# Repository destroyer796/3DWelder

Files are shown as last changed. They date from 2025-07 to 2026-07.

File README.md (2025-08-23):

# 3DWelder
This is an overbuilt 3D pen designed to be used for "welding" 3D printed parts together using 1.75mm filament. This project is funded by [Hack Club](https://hackclub.com/) as a part of the [Highway](https://highway.hackclub.com/) program.

Keep in mind for time being PCB is not working, I'll update soon.

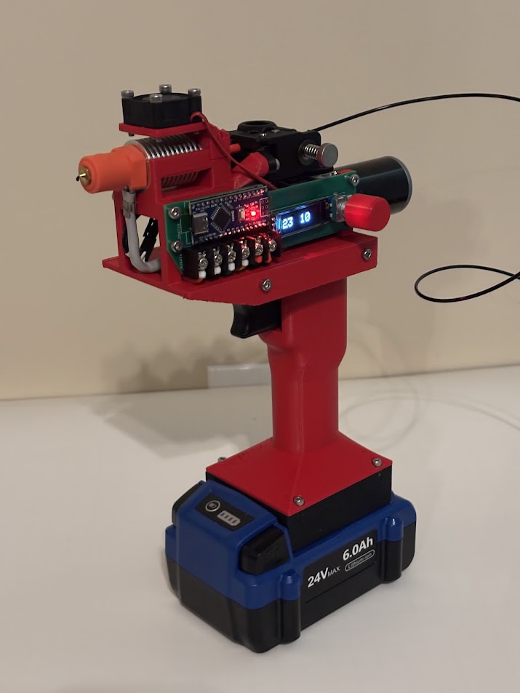
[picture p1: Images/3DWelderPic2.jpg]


This design uses a CHC Pro hotend and a custom Orbiter extruder adapted to use a DC motor. This DC motor's speed is controlled by a drill trigger adapted into the handle. It has a small screen and a rotary encoder for adjusting and showing the temperature target. The whole thing is powered by a drill battery to make it more portable and easier to use. This project is currently completely untested.

## Why?
So, why did I choose to make this ridiculous thing anyways? Well, the best way to join 3D printed parts together if they can't be screwed is by literally joining them together with the same plastic they're made of. This can be very difficult with a normal 3D pen though, as they're quite low powered and actually can't even melt many higher temperature plastics. I wanted a solution to this, so I decided to basically make a regular 3D printer extruding setup, but make it portable. It has some other uses aswell, if you use EVA filament, it could function essentially as a hot glue gun. It could also theoretically be used as a 3D pen, but not that well.

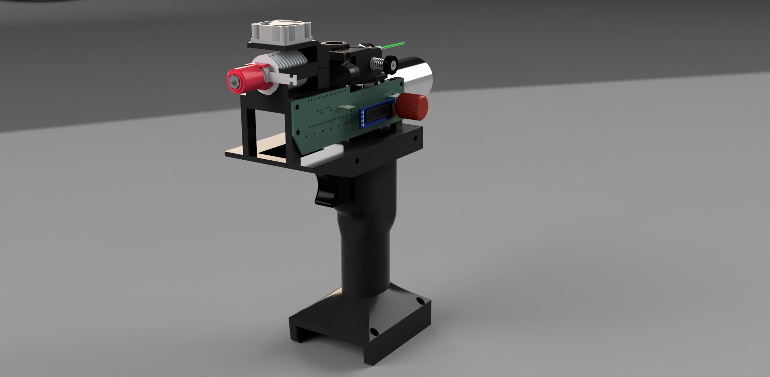
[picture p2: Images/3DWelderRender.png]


## PCB
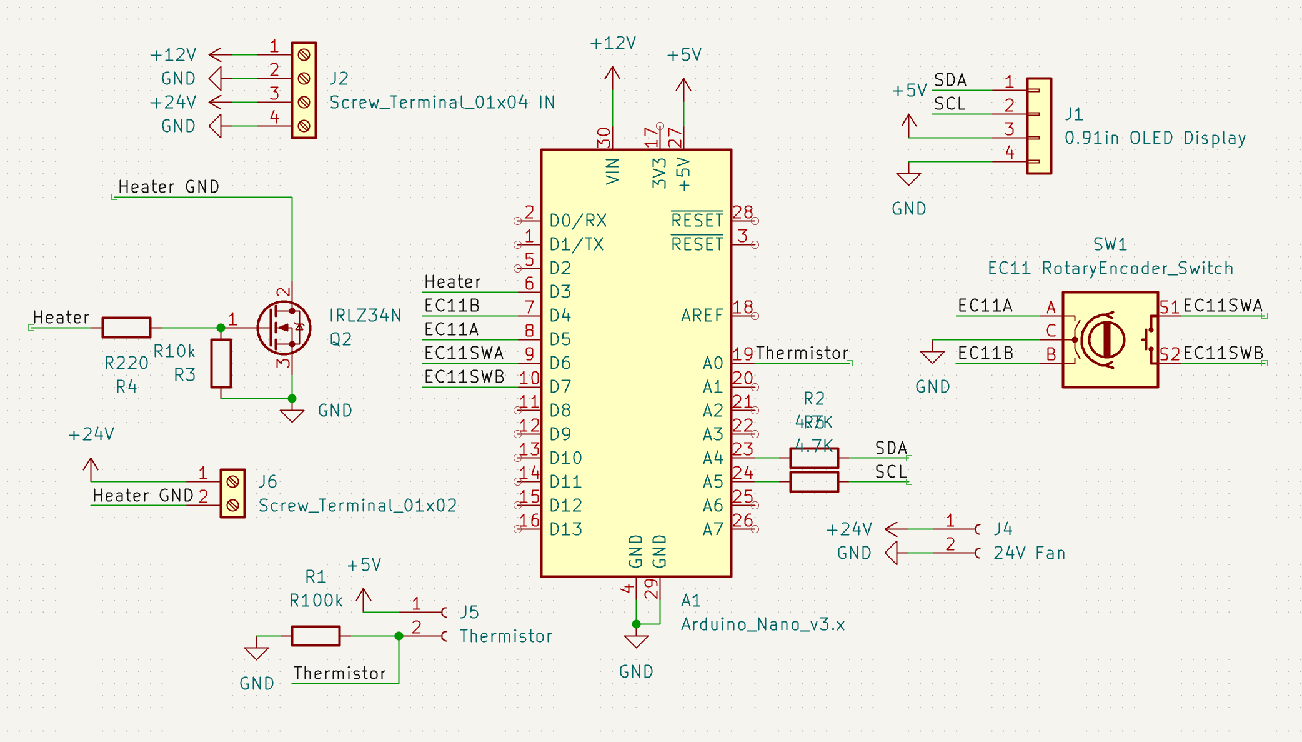
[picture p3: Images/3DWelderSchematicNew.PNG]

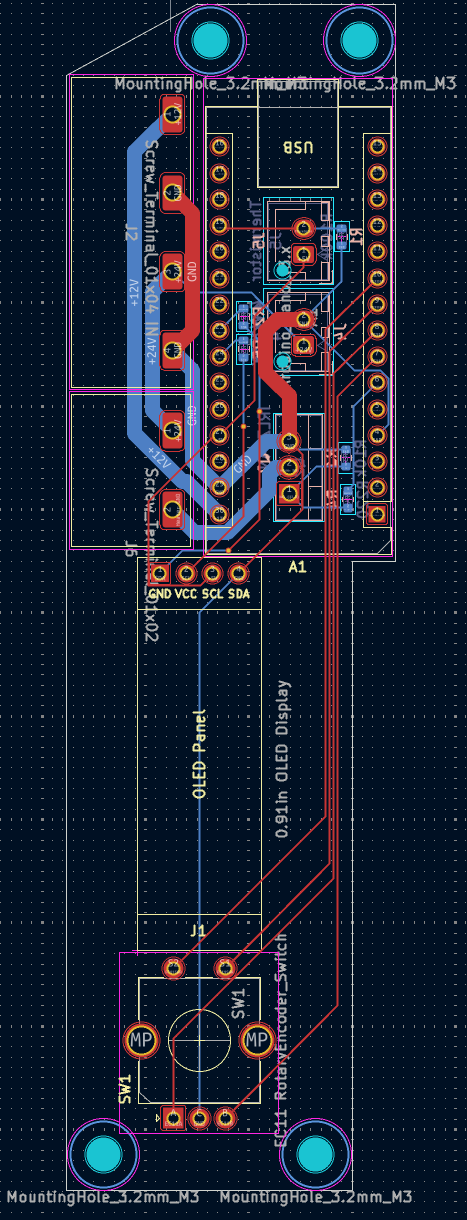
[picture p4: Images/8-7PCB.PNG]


The pcb was designed using KiCad, and it is only 2 layers. The pcb controlls everything except for voltage control and the motor, which is controlled by the drill trigger. It uses screw terminals and jst-xh connections. The brains of the whole thing is an Arduino Nano.

## Wiring/Assembly
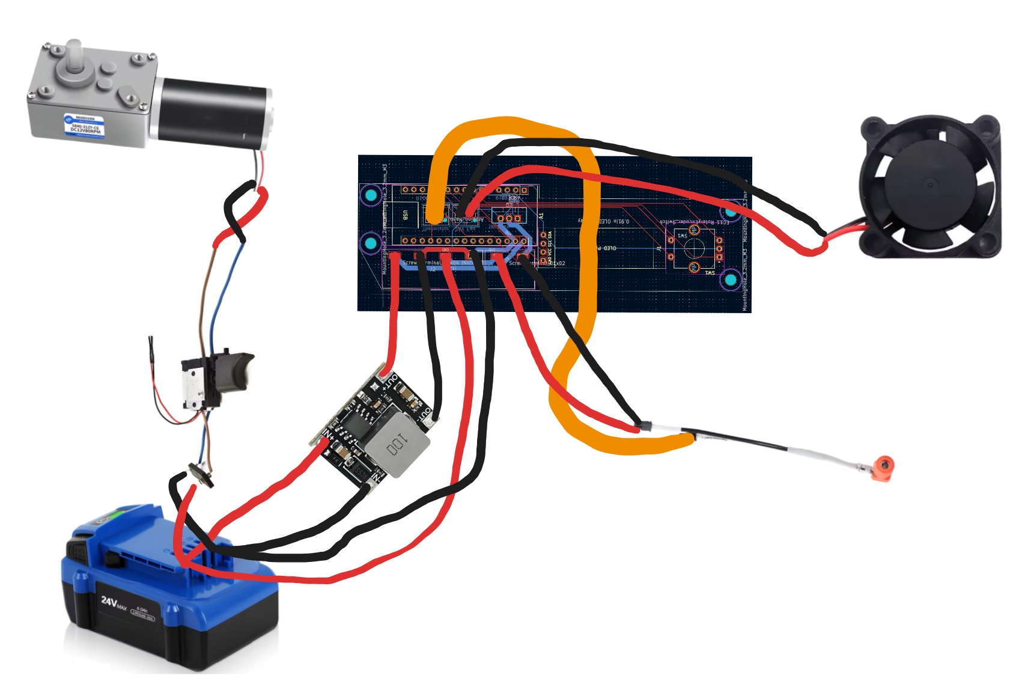
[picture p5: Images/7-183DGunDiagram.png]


All 3D printed parts screw together using M3 heatset inserts and various M3/M4 screws. For wiring, 2 spade connectors are used as terminals on the battery. From there, there's 2 ways of wiring everything else. You can either put the buck converter inside the space above the battery, then have wires coming off of that to the drill trigger and pcb, or have the buck converter up by the pcb, then have wires going back down to the drill trigger. Having the Buck converter in the handle is much cleaner, but may be very difficult to fit inside that small space.

## Code
<details>
  <summary>
    Arduino Code
  </summary>
  
  ~~~
  #include <PID_v1.h>
  #include <Adafruit_SSD1306.h>
  #include <Adafruit_GFX.h>
  #include <Wire.h>
  
  //Defines screen width/height
  #define SCREEN_WIDTH 128
  #define SCREEN_HEIGHT 32
  
  //Not using a reset pin
  #define OLED_RESET -1
  
  //Creates a display named display, gives it parameters
  Adafruit_SSD1306 display(SCREEN_WIDTH, SCREEN_HEIGHT, &Wire, OLED_RESET);
  
  // EC11 code
  const int EC11PinA = 8;
  const int EC11PinB = 7;
  volatile in encoderPos = 0;
  in lastEncoded = 0;
  
  /* -----------  USER SETTINGS  ----------- */
  const int   thermistorPin   = A0;
  const int   heaterPin       = 6;     // PWM pin
  const int   statusLedPin    = 13;    // Built‑in LED on most Arduinos
  const float R_FIXED         = 100000.0;   // 100 kΩ divider resistor
  
  // Steinhart–Hart coefficients for Semitec 104GT‑2 / 104NT
  const float A = 1.009249522e-3;
  const float B = 2.378405444e-4;
  const float C = 2.019202697e-7;
  
  // PID tuning
  double Kp = 4.0, Ki = 0.3, Kd = 12.0;
  
  /* Temperature targets */
  double setpointC   = 60.0;   // Desired temperature
  const double MAX_TEMP_C      = 300.0;   // Hard safety limit
  const double MIN_VALID_VOLT  = 0.10;   // Thermistor‑open detection
  
  /* -----------  GLOBALS  ----------- */
  double inputC, outputPWM;          // For PID library
  PID myPID(&inputC, &outputPWM, &setpointC, Kp, Ki, Kd, DIRECT);
  
  enum FaultState { OK, OVER_TEMPERATURE, SENSOR_ERROR };
  FaultState fault = OK;
  
  /* Timing helpers */
  unsigned long lastBlink   = 0;
  bool          ledState    = false;
  
  void setup() {
    //Start I2C
    Wire.begin();
  
    // Initializes display using I2C address 0x3C, if it fails it prints error message
    // Switchcapvcc thing tells it that display has internal voltage regulator
    if (!display.begin(SSD1306_SWITCHCAPVCC, 0x3C)) {
      Serial.begin(9600);
      Serial.println(F("SSD1306 allocation failed"));
      for (;;);
    }
  
    //Display test commands
    display.clearDisplay(); // Clears display
    display.setTextSize(1); // Sets text size, 1 = 6/8 pixels, 5/7 without spacing, 2 = 2x, 3 = 3x
    display.setTextColor(SSD1306_WHITE); // Set white text
    display.setCursor(0,0); // Sets cursor to top-left
    display.println(F("Hello SH-S091!")); // Print message to display buffer
    display.display(); // Push everything in buffer to scren
    // display.setFont(), allows you to change fonts, need to install them
    // display.fillRect(x, y, width, height, SSD1306_BLACK) draws a black rect, way to clear part of screen
  
    //EC11 Code
    pinMode(EC11PinA, INPUT_PULLUP);
    pinMode(EC11PinB, INPUT_PULLUP);
    attachInterrupt(digitalPinToInterrupt(EC11PinA), updateEncoder, CHANGE);
    attachInterrupt(digitalPinToInterrupt(EC11PinB), updateEncoder, CHANGE);

    pinMode(heaterPin,   OUTPUT);
    pinMode(statusLedPin, OUTPUT);
    Serial.begin(9600);
  
    myPID.SetOutputLimits(0, 255);
    myPID.SetSampleTime(250);          // 4 Hz PID updates
    myPID.SetMode(AUTOMATIC);
  }
  
  void loop() {
    //EC11 Code
    static int lastPos = 0;
    if (encoderPos != lastPos) {
      Serial.print("Value: ");
      Serial.println(encoderPos);
  
      display.fillRect(0, 0, 64, 32, SSD1306_BLACK);
      display.setTextSize(1);
      display.setTextColor(SSD1306_WHITE);
      display.setCursor(0,0);
      display.println(F(encoderPos));
      display.display
  
      lastPos = encoderPos;
    }

    /* ---------- Read thermistor ---------- */
    int   adc = analogRead(thermistorPin);
    float v   = adc * 5.0 / 1023.0;
  
    /* Sensor fault check */
    if (v < MIN_VALID_VOLT)  fault = SENSOR_ERROR;
  
    /* Convert to °C if no sensor fault */
    if (fault == OK) {
      double R = R_FIXED * (5.0 / v - 1.0);
      double lnR = log(R);
      double tempK = 1.0 / (A + B*lnR + C*lnR*lnR*lnR);
      inputC = tempK - 273.15;
  
      /* Over‑temperature check */
      if (inputC >= MAX_TEMP_C) fault = OVER_TEMPERATURE;
    }
  
    /* ---------- Safety Handling ---------- */
    if (fault != OK) {
      myPID.SetMode(MANUAL);       // Freeze PID
      outputPWM = 0;               // Heater OFF
      analogWrite(heaterPin, 0);
    } else {
      myPID.Compute();             // Let PID calculate outputPWM
      analogWrite(heaterPin, (int)outputPWM);
    }
  
    /* ---------- Status LED ----------
       • ON  …… actively heating (PWM > 0)
       • Slow blink …… at set‑point (PID output ~0)
       • Fast blink …… fault
    ---------------------------------- */
    unsigned long now = millis();
    unsigned long blinkPeriod =
        (fault != OK)          ? 150 :        // fast blink on fault
        (outputPWM < 2)        ? 800 :        // slow blink at set‑point
                                 0;           // solid ON while heating
  
    if (blinkPeriod == 0) {
      digitalWrite(statusLedPin, HIGH);
    } else if (now - lastBlink >= blinkPeriod) {
      ledState = !ledState;
      digitalWrite(statusLedPin, ledState);
      lastBlink = now;
    }
  
    /* ---------- Serial Monitor ---------- */
    Serial.print("Temp: ");
    Serial.print((fault == OK) ? inputC : NAN);
    Serial.print(" °C | PWM: ");
    Serial.print(outputPWM);
    Serial.print(" | Fault: ");
    Serial.println(
        (fault == OK) ? "None" :
        (fault == OVER_TEMPERATURE) ? "Over-Temp" : "Sensor Error");

    // Shows temp on display
    display.fillRect(64, 0, 64, 32, SSD1306_BLACK);
    display.setTextSize(1);
    display.setTextColor(SSD1306_WHITE);
    display.setCursor(64,0);
    display.println(F(inputC));
    display.display
  }
  
  //EC11 code, runs everytime a change in position is detected
  void updateEncoder() {
    int MSB = digitalREad(EC11PinA);
    int LSB = digitalRead(EC11PinB);
  
    int encoded = (MSB << 1) | LSB;
    int sum = (lastEncocded << 2) | encoded;
  
    //Clockwise
    if (sum == 0b1101 || sum == 0b0100 || sum == 0b0010 || sum == 0b1011) {
      encoderPos += 5;
    }
    //Counter-Clockwise
    if (sum == 0b1110 || sum == 0b0111 || sum == 0b0001 || sum == 0b1000) {
      encoderPos -= 5;
    }
  
    lastEncoded = encoded
  }
  ~~~

</details>

This is the firmware to be uploaded to the Arduino Nano. It's purpose is for PID control of the heater via the thermistor readings and mosfet. It has temperature control via the EC11 rotary encoder, and the temperature target and current temperature are displayed on the 0.91 inch OLED screen.

## BOM

| Item | Quantity | Price | Source | Notes | Owned/Buying |
|---|---|---|---|---|---|
| Drill Trigger | 1 | $3.57 | [Aliexpress](https://www.aliexpress.com/item/3256806562336203.html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) | For regulating motor | Buying |
| CHC Pro | 1 | $22.42 | [Aliexpress](https://www.aliexpress.com/item/3256806914810913.html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) | Hotend | Buying |
| Screw Terminal 4P | 1 | $2.50 | [Aliexpress](https://www.aliexpress.com/item/3256807282935438.html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) | 7.62mm pitch, Power inputs | Buying |
| Screw Terminal 2P | 1 | $1.87 | [Aliexpress](https://www.aliexpress.com/item/3256807282935438.html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) | 7.62mm pitch, Heater outputs | Buying |
| 2510 24V Fan | 1 | $2.08 | [Aliexpress](https://www.aliexpress.com/item/3256807251337149.html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) | Cools hotend | Owned |
| EC11 Rotary Encoder | 1 | $3.08 | [Aliexpress](https://www.aliexpress.com/item/3256805796819763.html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) | For controlling temp | Buying |
| I2C OLED | 1 | $1.85 | [Aliexpress](https://www.aliexpress.com/item/3256806179530924.html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) | 0.91in, Displays target/current temp | Buying |
| TO-220 Radiator | 1 | $1.94 | [Aliexpress](https://www.aliexpress.com/item/2255800003999447.html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) | Cools mosfet | Buying |
| IRLZ34NPBF Mosfet | 1 | $3.20 | [Aliexpress](https://www.aliexpress.com/item/3256808552158121.html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) | TO-220, Regulates hotend heater | Buying |
| 24V-12V Buck Converter | 1 | $4.12 | [Aliexpress](https://www.aliexpress.com/item/3256805319593185.html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) | Converts battery 24V to 12V for Arduino | Buying |
| DC Motor | 1 | $13.35 | [Aliexpress](https://www.aliexpress.com/item/3256807142640791.html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) | 24V, Worm gear, 27rpm, drives extruder | Buying |
| Kobalt 24V Battery | 1 | $28.35 | [Aliexpress](https://www.aliexpress.com/item/3256808341351094.html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) | Any Ah, mines 6.0Ah, Powers whole thing | Buying |
| 100k Resistor | 1 | $1.27 | [Aliexpress](https://www.aliexpress.us/item/3256805491339263.html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) | For thermistor logic | Owned |
| 10k Resistor | 1 | $1.34 | [Aliexpress](https://www.aliexpress.us/item/3256805491339263.html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) | Heater gate pulldown | Owned |
| 220R Resistor | 1 | $1.35 | [Aliexpress](https://www.aliexpress.us/item/3256805491339263.html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) | Heater gate drive | Owned |
| 2 Pin JST XH Female | 2 | $2.37 | [Aliexpress](https://www.aliexpress.com/item/3256803235887618.html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) | For fan and thermistor | Owned |
| 18 AWG Wire | ~2 meters | $2.11 | [Aliexpress](https://www.aliexpress.com/item/3256806379805687.html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) | Wiring everything | Owned |
| Arduino Nano | 1 | $2.94 | [Aliexpress](https://www.aliexpress.com/item/3256806587205161.html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) | Type C, Microprocessor | Buying |
| M3 Heatset Inserts | ~18 | $2.05 | [Aliexpress](https://www.aliexpress.com/item/3256803396040989.html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) | M3x5x4, Gives 3D printed parts threads | Owned |
| M3x6 Screws | ~11 | $2.04 | [Aliexpress](https://www.aliexpress.com/item/3256806983352954.html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) | For mounting pcb, battery terminal, and handle | Owned |
| M3x8 Screws | ~2 | $2.14 | [Aliexpress](https://www.aliexpress.com/item/3256806983352954.html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) | For Orbiter mount | Owned |
| M3x10 Screws | ~4 | $1.38 | [Aliexpress](https://www.aliexpress.com/item/3256805692722422.html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) | For mounting Hotend mount and hotend clamp | Owned |
| M4x8 Screws | 8 | $2.03 | [Aliexpress](https://www.aliexpress.com/item/3256806983352954.html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) | For motor mounting | Owned |
| Orbiter Gears | 1 | $23.32 | [Aliexpress](https://www.aliexpress.com/item/3256802185372532.html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) | Extruder drive gears | Buying |
| Orbiter Handle Shell | 1 | $3.17 | [Aliexpress](https://www.aliexpress.com/item/3256802185372532.html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) | Extruder lever + shaft | Buying |
| Orbiter Handle Screw | 1 | $2.67 | [Aliexpress](https://www.aliexpress.com/item/3256802185372532.html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) | Extruder lever screw/spring | Buying |
| Alternative Full Orbiter | 1 | $30.30 | [Aliexpress](https://www.aliexpress.us/item/3256803143364574.html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) | Around same price as above but full kit, worse parts | NOT Buying |
| PTFE Tube | 1 | $1.83 | [Aliexpress](https://www.aliexpress.com/item/3256808595111724.html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) | Between extruder and hotend, need very little | Owned |
| Spade Terminals | 2 | $2.38 | [Aliexpress](https://www.aliexpress.com/item/3256802579044914.html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) | For battery connection | Owned |
| Custom PCB | 1 | $8.52 | [JLC PCB](https://jlcpcb.com/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) | For connecting all components |

Total(No shipping/taxes): $148.12   <br>
My Total: $157.54 (with shipping/taxes, excluding owned items)

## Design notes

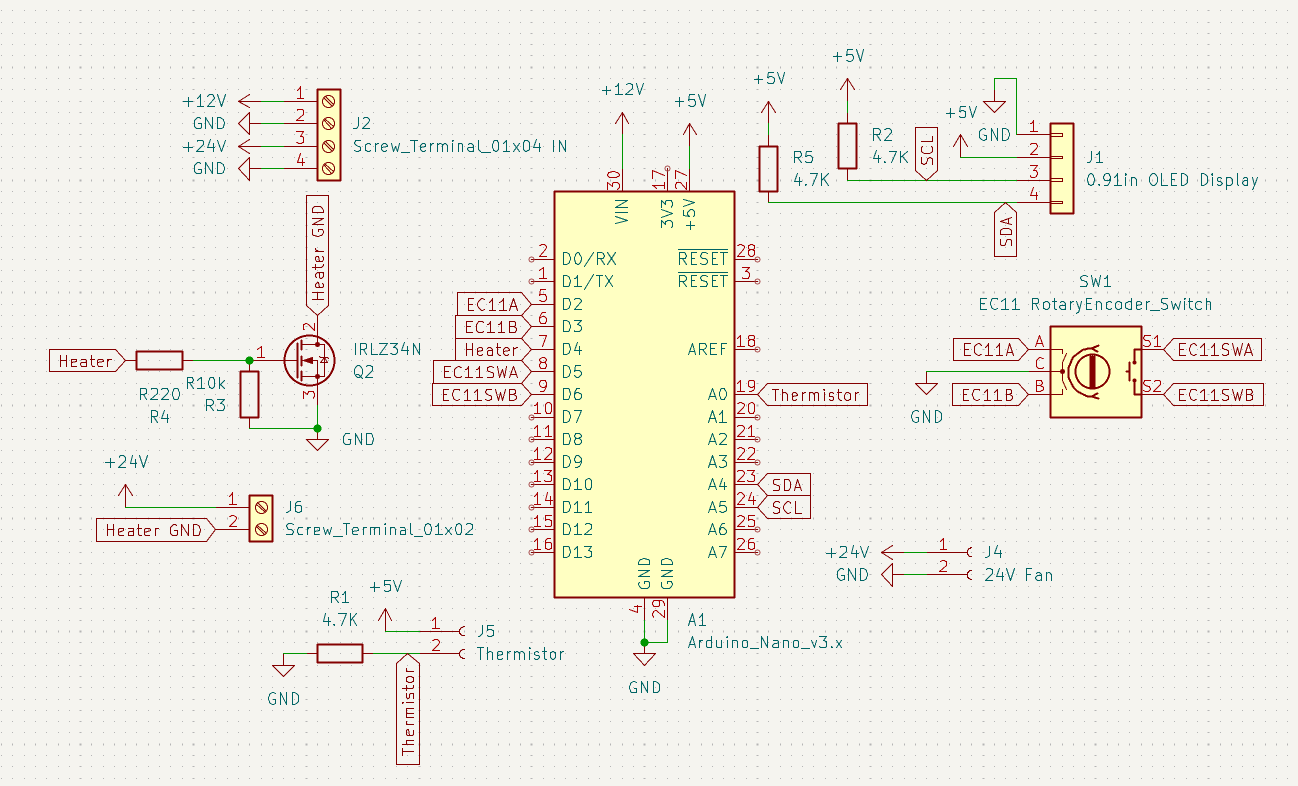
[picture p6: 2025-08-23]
Images/3DWelderSchematicPicV3.PNG

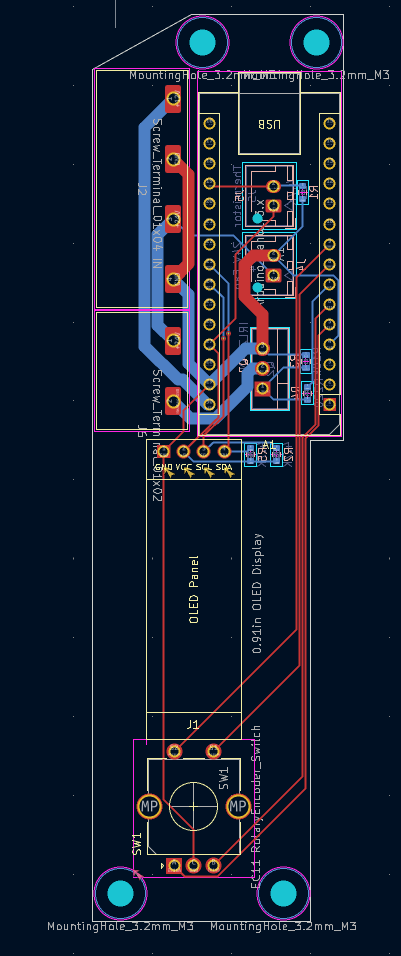
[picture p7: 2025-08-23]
Images/3DWelderPCBPicV3.PNG

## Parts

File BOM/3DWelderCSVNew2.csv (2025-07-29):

Item | Quantity | Price(no shipping/taxes) | Source | Notes | Owned/Buying | Amazon Link(faster shipping)
Drill Trigger | 1 | $3.57 | https://www.aliexpress.com/item/3256806562336203.html?mp=1 | For regulating motor | Buying | https://www.amazon.com/dp/B07QLYC192?ref=ppx_yo2ov_dt_b_fed_asin_title
CHC Pro | 1 | $22.42 | https://www.aliexpress.com/item/3256806914810913.html?mp=1 | Hotend | Buying
Screw Terminal 4P | 1 | $2.50 | https://www.aliexpress.com/item/3256807282935438.html?mp=1 | 7.62mm pitch, Power inputs | Buying
Screw Terminal 2P | 1 | $1.87 | https://www.aliexpress.com/item/3256807282935438.html?mp=1 | 7.62mm pitch, Heater outputs | Buying
2510 24V Fan | 1 | $2.08 | https://www.aliexpress.com/item/3256807251337149.html?mp=1 | Cools hotend | Owned
EC11 Rotary Encoder | 1 | $3.08 | https://www.aliexpress.com/item/3256805796819763.html?mp=1 | For controlling temp | Owned
I2C OLED | 1 | $1.85 | https://www.aliexpress.com/item/3256806179530924.html?mp=1 | 0.91in, Displays target/current temp | Owned
TO-220 Radiator | 1 | $1.94 | https://www.aliexpress.com/item/2255800003999447.html?mp=1 | Cools mosfet | Buying
IRLZ34NPBF Mosfet | 1 | $3.20 | https://www.aliexpress.com/item/3256808552158121.html?mp=1 | TO-220, Regulates hotend heater | Buying | https://www.amazon.com/dp/B0CBKGP1GV?ref=ppx_yo2ov_dt_b_fed_asin_title&th=1
24V-12V Buck Converter | 1 | $4.12 | https://www.aliexpress.com/item/3256805319593185.html?mp=1 | Converts battery 24V to 12V for Arduino | Buying | https://www.amazon.com/dp/B0DBVYP91F?ref=ppx_yo2ov_dt_b_fed_asin_title&th=1
DC Motor | 1 | $13.35 | https://www.aliexpress.com/item/3256807142640791.html?mp=1 | 24V, Worm gear, 27rpm, drives extruder | Buying | https://www.amazon.com/dp/B09HWYQSHF?ref=ppx_yo2ov_dt_b_fed_asin_title&th=1
Kobalt 24V Battery | 1 | $28.35 | https://www.aliexpress.com/item/3256808341351094.html?mp=1 | Any Ah, mines 6.0Ah, Powers whole thing | Buying
100k Resistor | 1 | $1.27 | https://www.aliexpress.us/item/3256805491339263.html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 | For thermistor logic | Buying | https://www.amazon.com/dp/B013B5587K?ref=ppx_yo2ov_dt_b_fed_asin_title
10k Resistor | 1 | $1.34 | https://www.aliexpress.us/item/3256805491339263.html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 | Heater gate pulldown | Buying | https://www.amazon.com/dp/B013B5587K?ref=ppx_yo2ov_dt_b_fed_asin_title
220R Resistor | 1 | $1.35 | https://www.aliexpress.us/item/3256805491339263.html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 | Heater gate drive | Buying | https://www.amazon.com/dp/B013B5587K?ref=ppx_yo2ov_dt_b_fed_asin_title
4.7K Resistor | 2 | $1.25 | https://www.aliexpress.us/item/3256805491339263.html?mp=1 | Pullups for I2C | Buying | https://www.amazon.com/dp/B013B5587K?ref=ppx_yo2ov_dt_b_fed_asin_title
2 Pin JST XH Female | 2 | $2.37 | https://www.aliexpress.com/item/3256803235887618.html?mp=1 | For fan and thermistor | Owned
18 AWG Wire | ~2 meters | $2.11 | https://www.aliexpress.com/item/3256806379805687.html?mp=1 | Wiring everything | Owned
Arduino Nano | 1 | $2.94 | https://www.aliexpress.com/item/3256806587205161.html?mp=1 | Type C, Microprocessor | Buying
M3 Heatset Inserts | ~18 | $2.05 | https://www.aliexpress.com/item/3256803396040989.html?mp=1 | M3x5x4, Gives 3D printed parts threads | Owned
M3x6 Screws | ~11 | $2.04 | https://www.aliexpress.com/item/3256806983352954.html?mp=1 | For mounting pcb, battery terminal, and handle | Owned
M3x8 Screws | ~2 | $2.14 | https://www.aliexpress.com/item/3256806983352954.html?mp=1 | For Orbiter mount | Owned
M3x10 Screws | ~4 | $1.38 | https://www.aliexpress.com/item/3256805692722422.html?mp=1 | For mounting Hotend mount and hotend clamp | Owned
M4x8 Screws | 8 | $2.03 | https://www.aliexpress.com/item/3256806983352954.html?mp=1 | For motor mounting | Owned
Orbiter Gears | 1 | $23.32 | https://www.aliexpress.com/item/3256802185372532.html?mp=1 | Extruder drive gears | Buying | https://www.amazon.com/dp/B09V29W7S5?ref=ppx_yo2ov_dt_b_fed_asin_title
Orbiter Handle Shell | 1 | $3.17 | https://www.aliexpress.com/item/3256802185372532.html?mp=1 | Extruder lever + shaft | Buying | https://www.amazon.com/dp/B0DP28ZTSL?ref=ppx_yo2ov_dt_b_fed_asin_title&th=1
Orbiter Handle Screw | 1 | $2.67 | https://www.aliexpress.com/item/3256802185372532.html?mp=1 | Extruder lever screw/spring | Not Buying
Alternative Full Orbiter | 1 | $30.30 | https://www.aliexpress.us/item/3256803143364574.html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 | Around same price as above but full kit, worse parts | NOT Buying
PTFE Tube | 1 | $1.83 | https://www.aliexpress.com/item/3256808595111724.html?mp=1 | Between extruder and hotend, need very little | Owned
Spade Terminals | 2 | $2.38 | https://www.aliexpress.com/item/3256802579044914.html?mp=1 | For battery connection | Owned
Custom PCB | 1 | $5.40 | https://jlcpcb.com/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 | For connecting all components | Buying
Total(No shipping/taxes): $148.12
My Total: $157.54 (with shipping/taxes, excluding owned items)

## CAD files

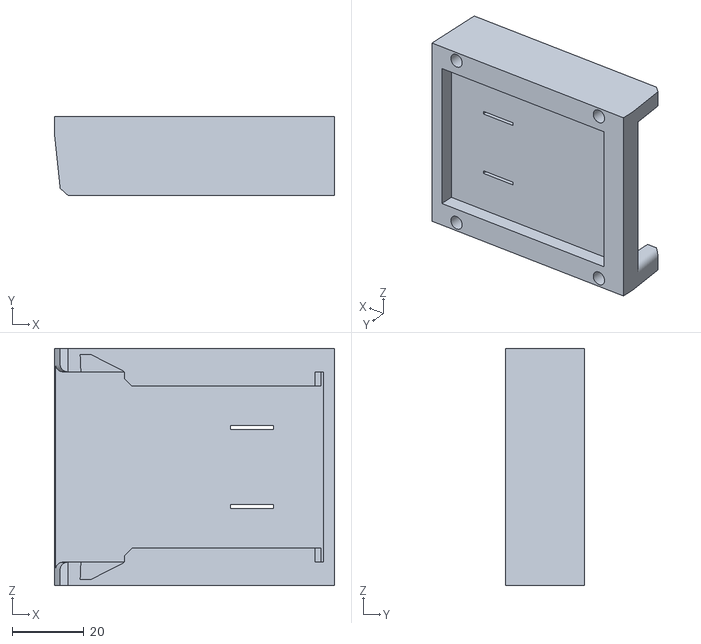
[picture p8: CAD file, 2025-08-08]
CAD/3DWelderBatteryAdapterV3.stl
77.9 x 22.0 x 66.0

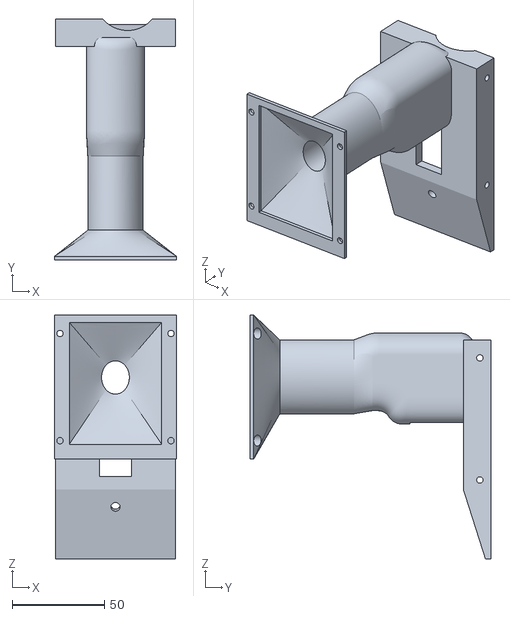
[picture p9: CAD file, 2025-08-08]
CAD/3DWelderHandleV3.stl
66.0 x 130.3 x 132.0

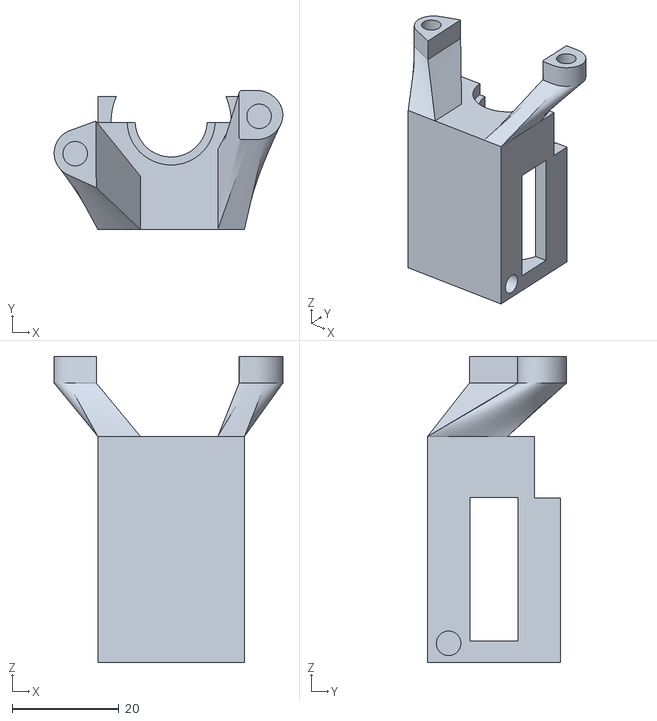
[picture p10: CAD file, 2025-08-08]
CAD/3DWelderCHCProMountV2.stl
42.9 x 26.1 x 57.4

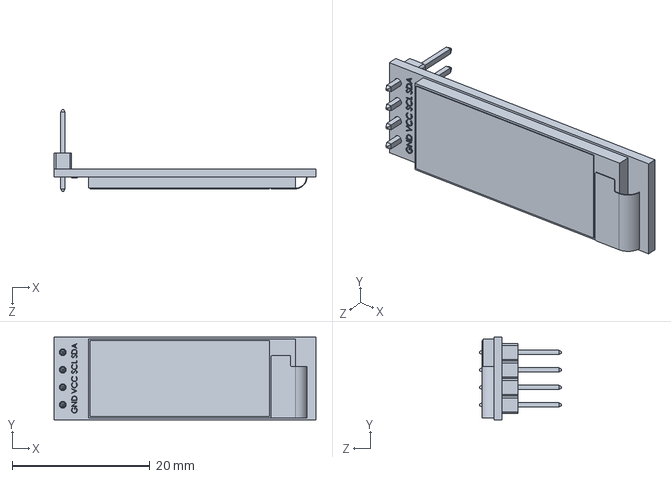
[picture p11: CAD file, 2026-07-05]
PCB/3D models/128x32-OLED.STEP
38.0 x 12.0 x 11.9 mm

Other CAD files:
CAD/3DWelderSTEPV4.step
PCB/3D models/KF7.62-4P.step
PCB/Kicad.step
CAD/3DWelderUpperBodyV2.step
PCB/3D models/KF7.62-2P.step
CAD/3DWelderSTEPV3.step
PCB/3D models/EC11.step
PCB/3D models/Arduino_NANO_CH340.step
PCB/3D models/EC11(1).step
CAD/3DWelderUpperBodyV2.stl

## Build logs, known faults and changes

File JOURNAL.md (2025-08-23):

---
title: "3DWelder"
author: "Liam Newbill"
description: "An overbuilt 3D pen using a CHC Pro and custom dc motor extruder powered by a power tool battery."
created_at: "2025-7-3"
---

This is my journal of all my work and time spend on this project. Total time: 68.5 hours.

## July 3rd: Pretty much just planning and some research for parts I could use (2.5 hours)
I did a lot of research into using a stepper motor powered extruder like a 3d printer but I realized that it would probably be simpler and cheaper to use a dc motor instead for this use case, I'm planning on using a 12v dc motor now. 
I'm thinking I'll use a 12v Dewalt battery or something and power this motor and an arduino nano off of it, I might add a boost converter to get 24v for the hotend or just run with 12v if I can get enough power. I need to do more research on that.
I think I'll do like a hot glue gun design with a trigger to vary the speed of the motor, and add a screen and dial for setting the temp.

[Motor](https://www.amazon.com/Greartisan-Geared-Turbine-Reduction-JSX330-370/dp/B0721W14ZN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)

## July 5th: Schematic Design and parts research (3 hours)
Today I fleshed out the whole electronics setup and made the schematic. I also researched thermal management solutions. My plan is to have a small heatsink on the mosfets and use a buck converter to get 12v from the 18v battery, then drive the hotend directly off the battery voltage.
I am now planning to use a 0.91 inch OLED display and EC11 rotary encoder for the temperature selection. I'll use the screen to display the temp, dial to adjust it and press the dial to put the gun to sleep, like keep the temp lower but not fully shut off.

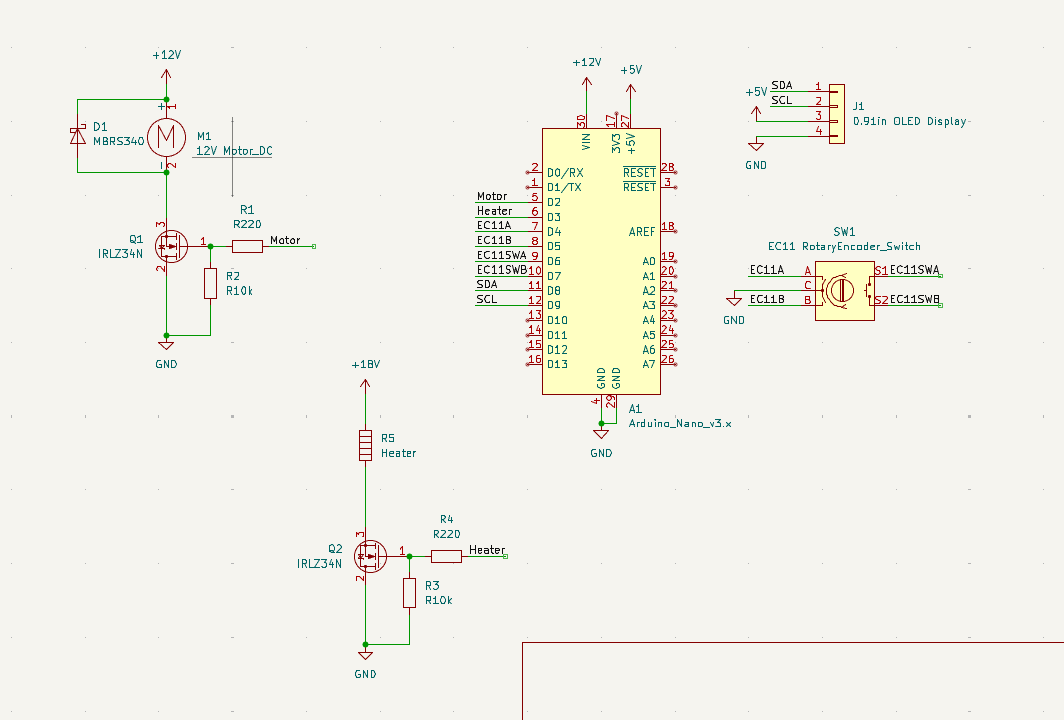
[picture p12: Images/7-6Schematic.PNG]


## July 6th/7th: Rethought schematic some, lots of CAD work, PCB design completed, got a semi-final BOM (12 hours)--Through midnight
This was a mega session, I have basically everything done except for the CAD, I still have to figure out how to do the battery though. This was some quite challenging CAD work, as it's a lot of weird parts and packaging is very challenging. This thing is going to be way bigger than I'd like, partially because the motor I chose is massive, but it's too late now to change it. I removed the mosfet control for the motor, that's now just done off of the drill trigger. It turns out, drill triggers are actually all in one speed controllers. For the extruder design, I've adapted the LDO Orbiter to work with the DC motor. I essentially cut out the gearing entirely so the motor just attaches straight to the drive gear. Unfortunately there wasen't really any good place to put the pcb, so there's just gonna be a huge box taking up most of the front, it's not elegant at all, but nothing about this thing is, so whatever. I'm really not looking forward to finishing the case and making the handle. Fitting that trigger in is going to be very difficult, as it's a weird geometry and I'm horrible at organic modelling. I can't decide if I want to just buy a battery adapter or make my own, the problem with buying one is I can't find any dimensions to mount it, so I think I'm just gonna have to figure out my own adapter. I'm regretting my choice of screw terminals for a lot of the connections, as they take up a ton of space. I'd like to keep them, but I might end up redesigning the pcb if I get tired of having that huge box.

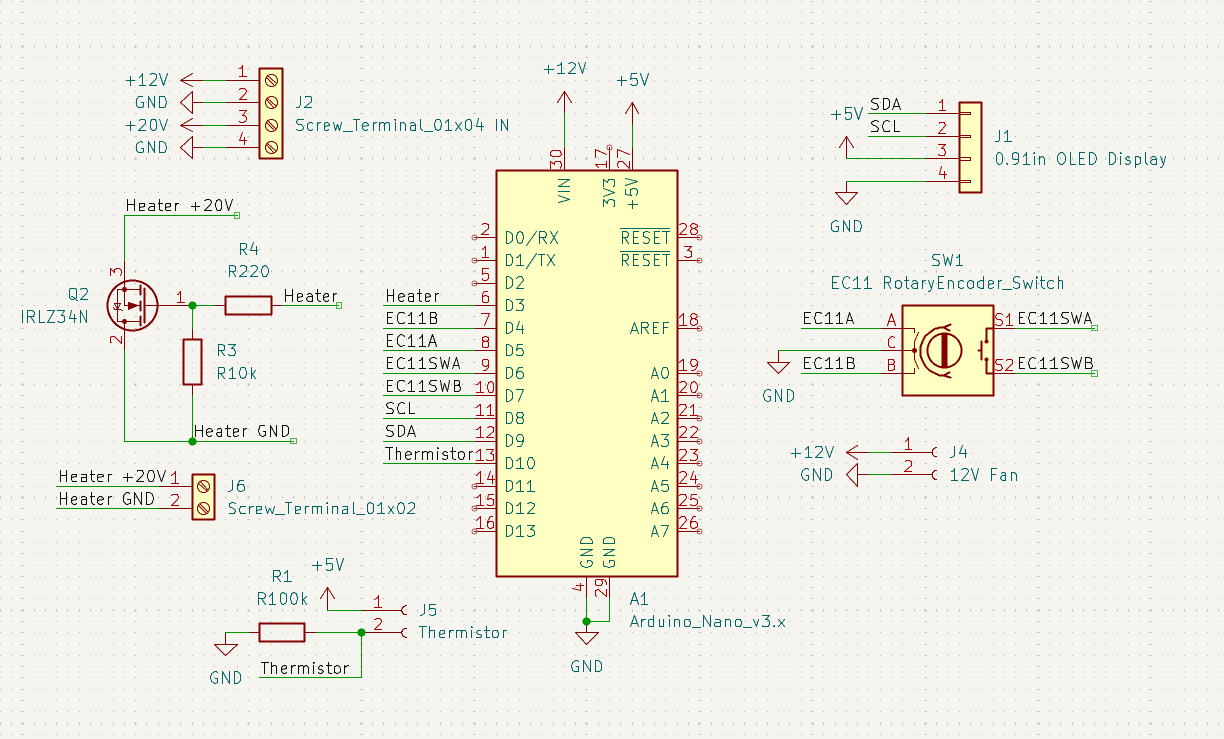
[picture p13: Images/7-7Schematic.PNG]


New schematic

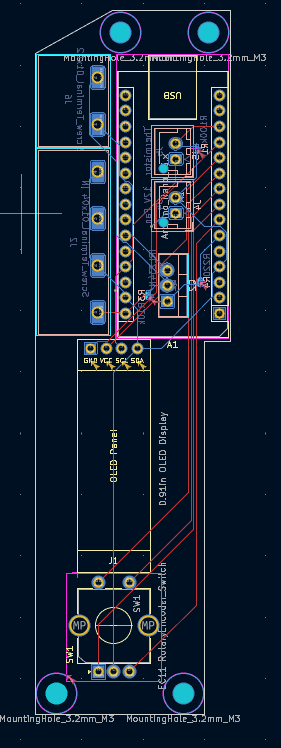
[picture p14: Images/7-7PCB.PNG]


PCB

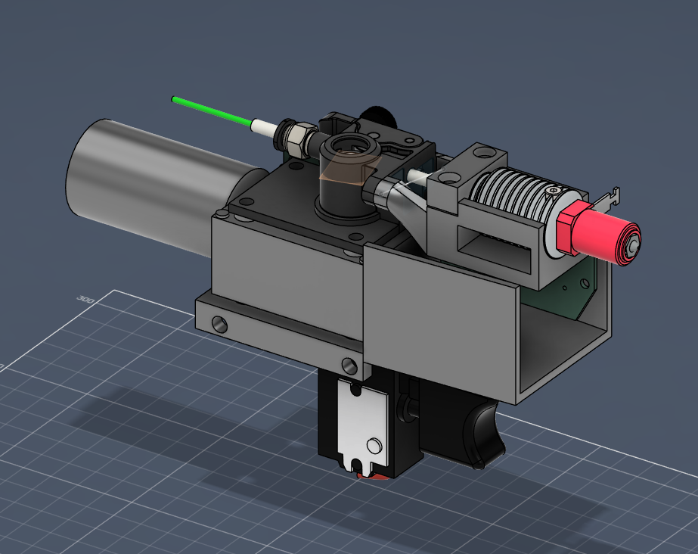
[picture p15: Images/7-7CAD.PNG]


CAD

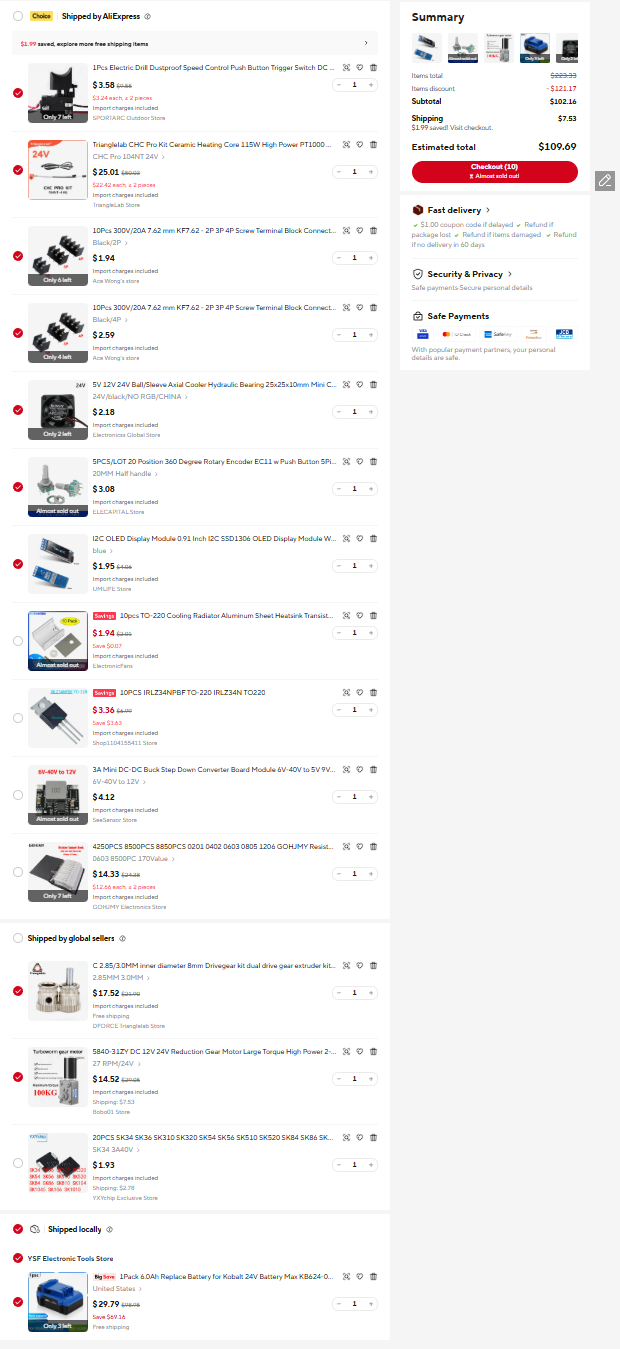
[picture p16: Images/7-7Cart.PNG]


Current BOM

## July 8/9th: Went through midnight again. Corrected schematic some, redid some of pcb routing, lots of CAD work (7 hours)
Adjusted the schematic because I realized I setup the diode wrong. I also redid some of the pcb design and added thicker traces for the power supply. Most of the time was spend on CAD, I created a battery mounting system, modelled the handle and mounting for the handle, added pcb mounting, and added a cooling fan mount for the extruder heatsink. The handle was quite a pain, but I think it turned out alright. I kept running into headaches because of my poor CAD habits, like not putting sketches under their proper component. This led to a lot of redoing stuff because I had to adjust things. I really need to work on keeping an organized timeline too, I kinda like to work without it but I should definately put more effort to learning Fusion stuff more. Anyways, I'm basically done with hardware now. The only thing left(hopefully) is adding a cosmetic shell, and coding.

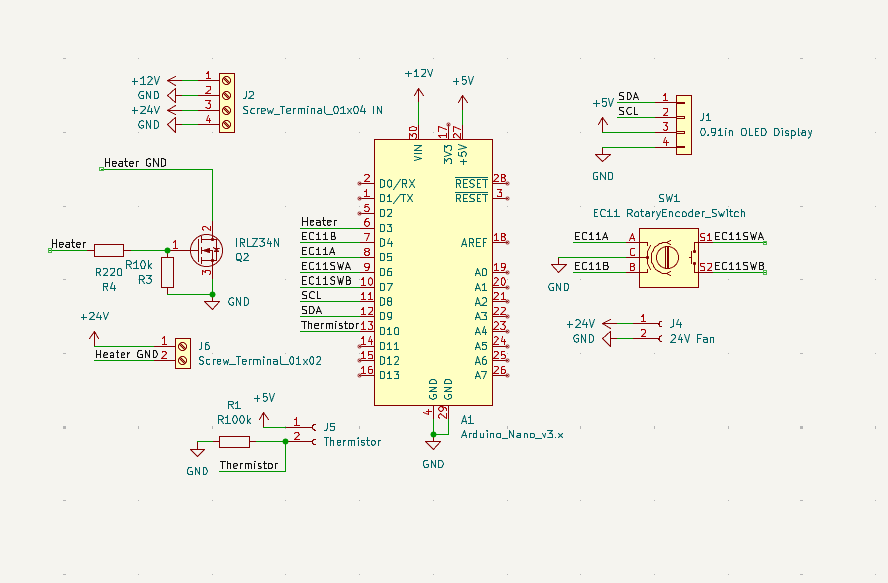
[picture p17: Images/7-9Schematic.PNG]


Schematic

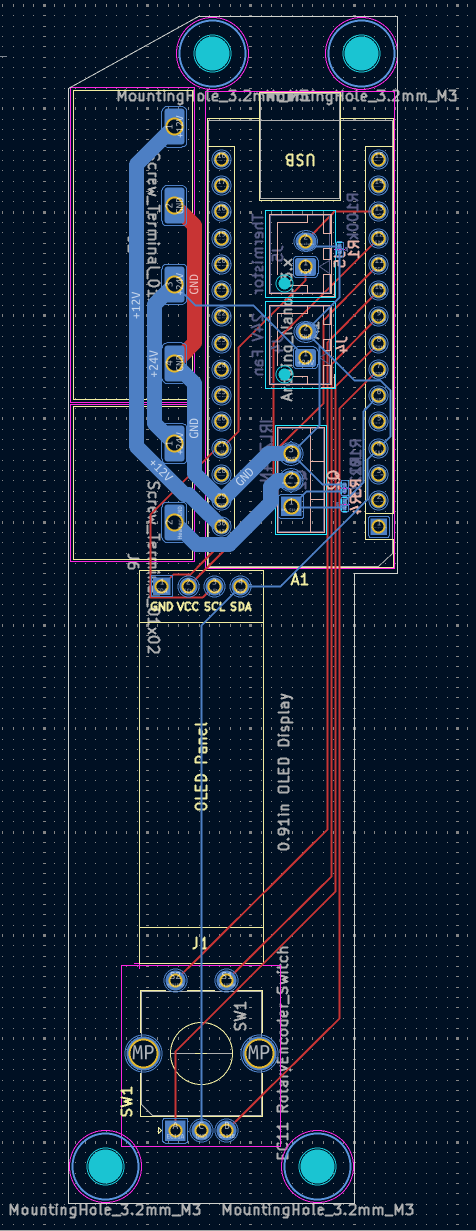
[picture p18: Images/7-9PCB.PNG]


PCB

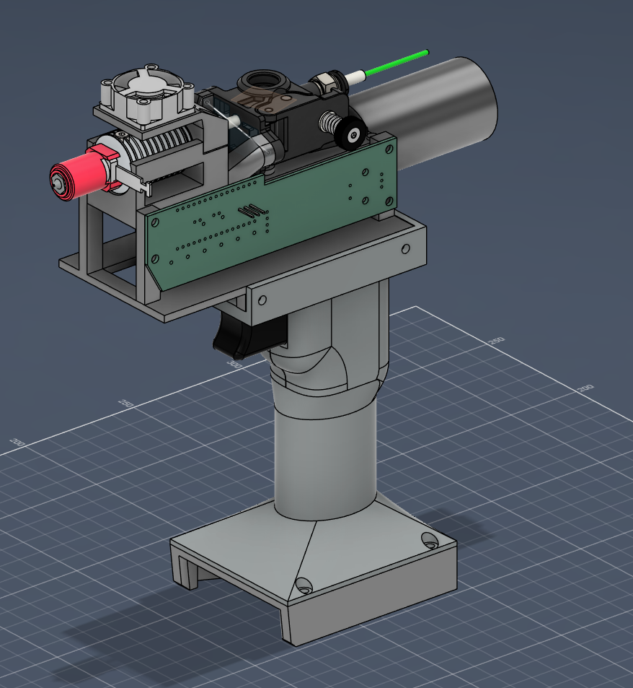
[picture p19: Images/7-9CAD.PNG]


CAD

## July 9th: Corrected one thing on schematic/pcb and wrote code (2.5 hours)
Today was mostly just coding, I wrote code for the pid control of the heater and got the rotary encoder stuff. I still need to do the screen and wrap it all together. I tried simulating some stuff in tinkercad to test the code but I couldn't figure out anything good for pid control testing so I gave up on that. I also just had to change the input pin for the thermistor and added some stuff to the schematic to represent the battery and buck converter. I'll add images of that in a future session when it's done.

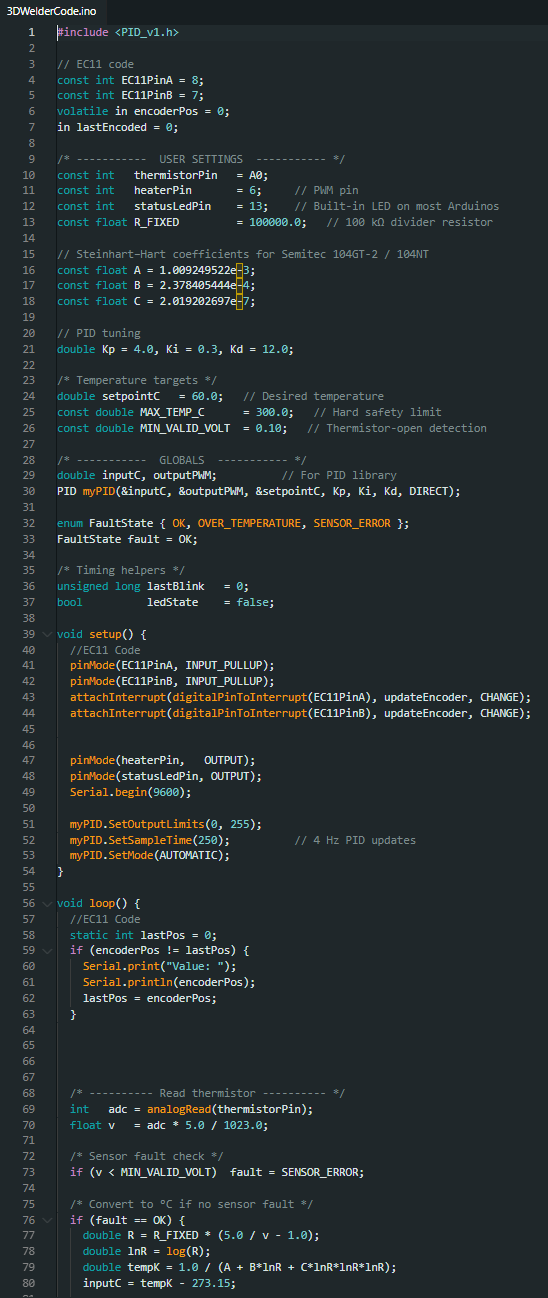
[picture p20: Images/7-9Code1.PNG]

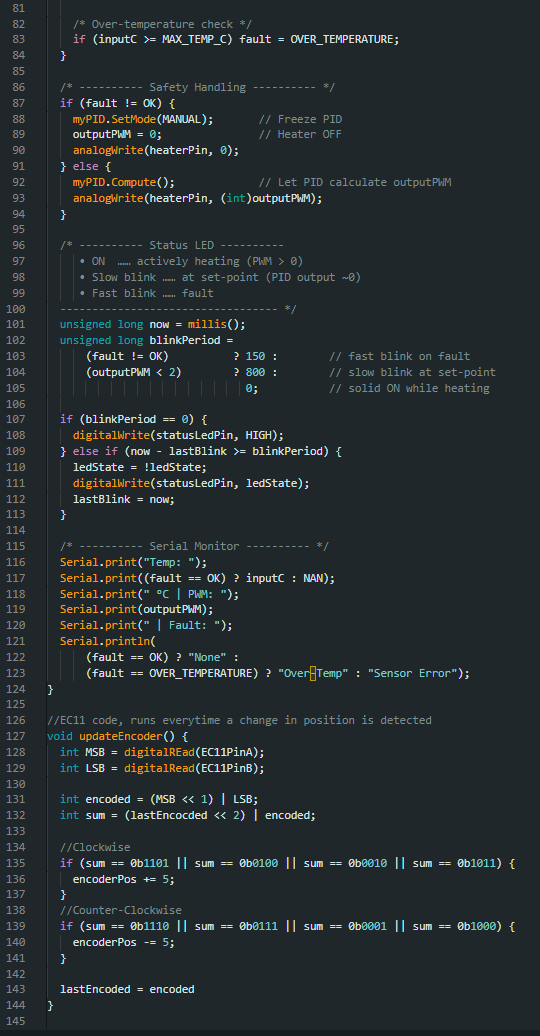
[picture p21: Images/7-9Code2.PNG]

Code

## July 17/18th: Went through midnight. Corrected screen pins to Arduino, small CAD detail coded screen, and BOM (6 hours)
Lots of small changes today, I realized the Oled was connected to the wrong pins on the arduino so I had to correct that. I added a little slope to the handle to route the wires through, and tried to work towards an enclosure but kinda gave up because I can't think of a good way to leave the extruder exposed enough, while still looking ok, plus I think it's cool exposed. Most of the time was spend on coding, I added code for the screen and updating it and stuff. It's pretty rough rn since I don't have anything to test it on, but it should work in theory. I made the whole BOM, everything is sourced from Aliexpress. It's around $150 for the whole thing, which I think is quite good, considering that included a lot of hardware most people probably have.

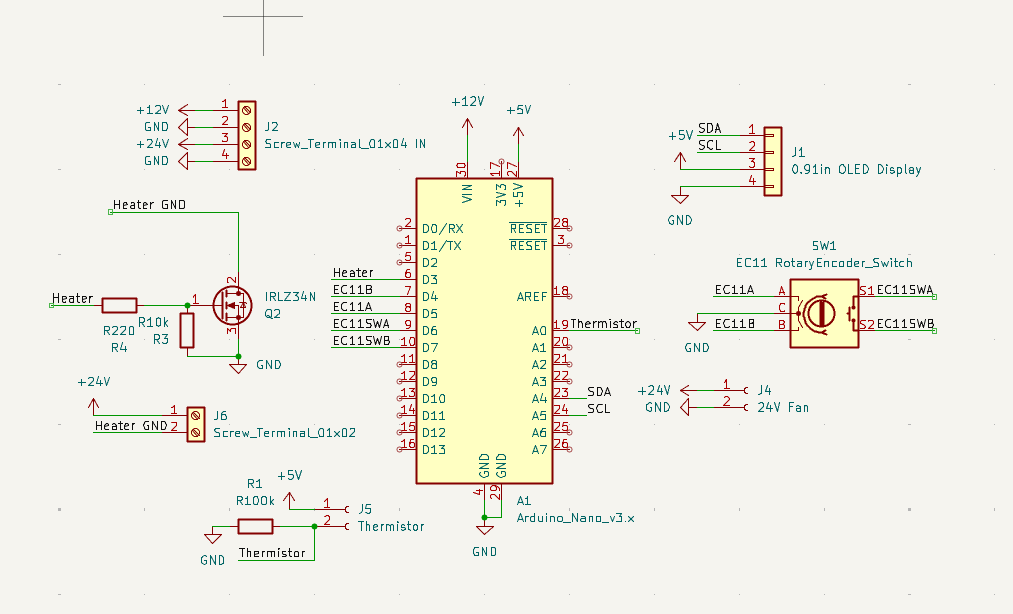
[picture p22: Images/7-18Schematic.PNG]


Schematic

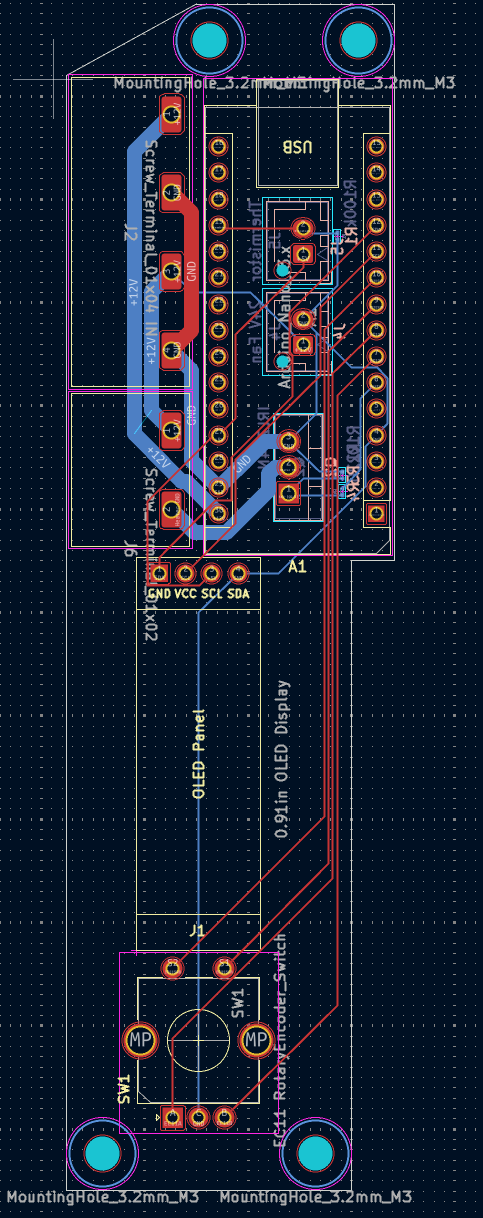
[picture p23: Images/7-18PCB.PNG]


PCB

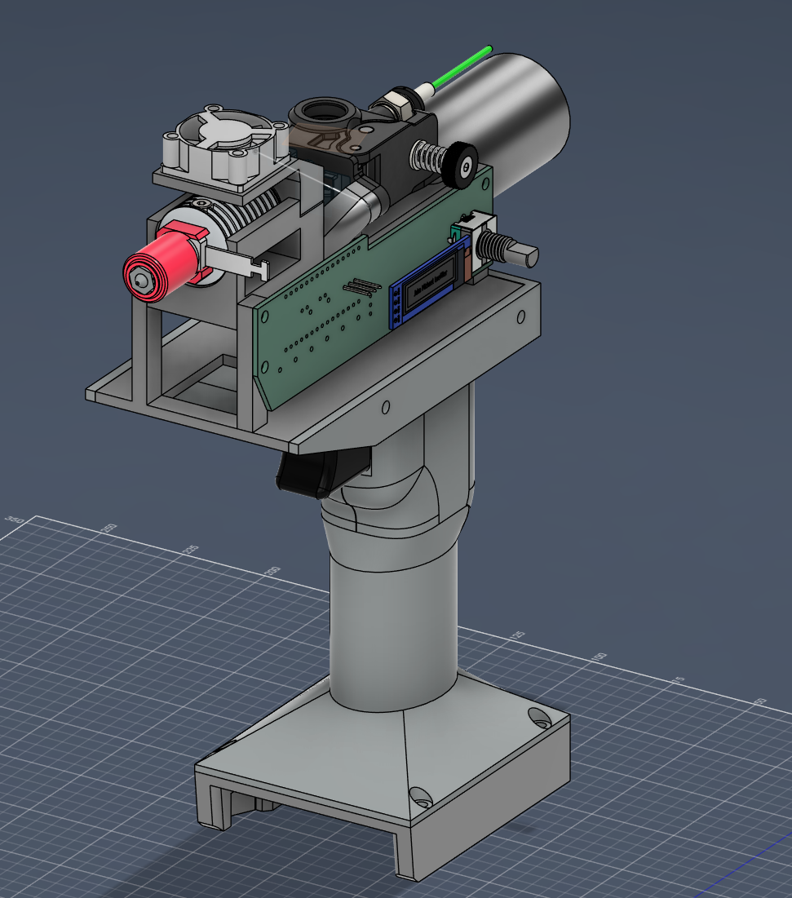
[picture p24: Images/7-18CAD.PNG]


CAD

<details>
  <summary>
    Arduino Code
  </summary>
  
  ~~~
  #include <PID_v1.h>
  #include <Adafruit_SSD1306.h>
  #include <Adafruit_GFX.h>
  #include <Wire.h>
  
  //Defines screen width/height
  #define SCREEN_WIDTH 128
  #define SCREEN_HEIGHT 32
  
  //Not using a reset pin
  #define OLED_RESET -1
  
  //Creates a display named display, gives it parameters
  Adafruit_SSD1306 display(SCREEN_WIDTH, SCREEN_HEIGHT, &Wire, OLED_RESET);
  
  // EC11 code
  const int EC11PinA = 8;
  const int EC11PinB = 7;
  volatile in encoderPos = 0;
  in lastEncoded = 0;
  
  /* -----------  USER SETTINGS  ----------- */
  const int   thermistorPin   = A0;
  const int   heaterPin       = 6;     // PWM pin
  const int   statusLedPin    = 13;    // Built‑in LED on most Arduinos
  const float R_FIXED         = 100000.0;   // 100 kΩ divider resistor
  
  // Steinhart–Hart coefficients for Semitec 104GT‑2 / 104NT
  const float A = 1.009249522e-3;
  const float B = 2.378405444e-4;
  const float C = 2.019202697e-7;
  
  // PID tuning
  double Kp = 4.0, Ki = 0.3, Kd = 12.0;
  
  /* Temperature targets */
  double setpointC   = 60.0;   // Desired temperature
  const double MAX_TEMP_C      = 300.0;   // Hard safety limit
  const double MIN_VALID_VOLT  = 0.10;   // Thermistor‑open detection
  
  /* -----------  GLOBALS  ----------- */
  double inputC, outputPWM;          // For PID library
  PID myPID(&inputC, &outputPWM, &setpointC, Kp, Ki, Kd, DIRECT);
  
  enum FaultState { OK, OVER_TEMPERATURE, SENSOR_ERROR };
  FaultState fault = OK;
  
  /* Timing helpers */
  unsigned long lastBlink   = 0;
  bool          ledState    = false;
  
  void setup() {
    //Start I2C
    Wire.begin();
  
    // Initializes display using I2C address 0x3C, if it fails it prints error message
    // Switchcapvcc thing tells it that display has internal voltage regulator
    if (!display.begin(SSD1306_SWITCHCAPVCC, 0x3C)) {
      Serial.begin(9600);
      Serial.println(F("SSD1306 allocation failed"));
      for (;;);
    }
  
    //Display test commands
    display.clearDisplay(); // Clears display
    display.setTextSize(1); // Sets text size, 1 = 6/8 pixels, 5/7 without spacing, 2 = 2x, 3 = 3x
    display.setTextColor(SSD1306_WHITE); // Set white text
    display.setCursor(0,0); // Sets cursor to top-left
    display.println(F("Hello SH-S091!")); // Print message to display buffer
    display.display(); // Push everything in buffer to scren
    // display.setFont(), allows you to change fonts, need to install them
    // display.fillRect(x, y, width, height, SSD1306_BLACK) draws a black rect, way to clear part of screen
  
    //EC11 Code
    pinMode(EC11PinA, INPUT_PULLUP);
    pinMode(EC11PinB, INPUT_PULLUP);
    attachInterrupt(digitalPinToInterrupt(EC11PinA), updateEncoder, CHANGE);
    attachInterrupt(digitalPinToInterrupt(EC11PinB), updateEncoder, CHANGE);

    pinMode(heaterPin,   OUTPUT);
    pinMode(statusLedPin, OUTPUT);
    Serial.begin(9600);
  
    myPID.SetOutputLimits(0, 255);
    myPID.SetSampleTime(250);          // 4 Hz PID updates
    myPID.SetMode(AUTOMATIC);
  }
  
  void loop() {
    //EC11 Code
    static int lastPos = 0;
    if (encoderPos != lastPos) {
      Serial.print("Value: ");
      Serial.println(encoderPos);
  
      display.fillRect(0, 0, 64, 32, SSD1306_BLACK);
      display.setTextSize(1);
      display.setTextColor(SSD1306_WHITE);
      display.setCursor(0,0);
      display.println(F(encoderPos));
      display.display
  
      lastPos = encoderPos;
    }

    /* ---------- Read thermistor ---------- */
    int   adc = analogRead(thermistorPin);
    float v   = adc * 5.0 / 1023.0;
  
    /* Sensor fault check */
    if (v < MIN_VALID_VOLT)  fault = SENSOR_ERROR;
  
    /* Convert to °C if no sensor fault */
    if (fault == OK) {
      double R = R_FIXED * (5.0 / v - 1.0);
      double lnR = log(R);
      double tempK = 1.0 / (A + B*lnR + C*lnR*lnR*lnR);
      inputC = tempK - 273.15;
  
      /* Over‑temperature check */
      if (inputC >= MAX_TEMP_C) fault = OVER_TEMPERATURE;
    }
  
    /* ---------- Safety Handling ---------- */
    if (fault != OK) {
      myPID.SetMode(MANUAL);       // Freeze PID
      outputPWM = 0;               // Heater OFF
      analogWrite(heaterPin, 0);
    } else {
      myPID.Compute();             // Let PID calculate outputPWM
      analogWrite(heaterPin, (int)outputPWM);
    }
  
    /* ---------- Status LED ----------
       • ON  …… actively heating (PWM > 0)
       • Slow blink …… at set‑point (PID output ~0)
       • Fast blink …… fault
    ---------------------------------- */
    unsigned long now = millis();
    unsigned long blinkPeriod =
        (fault != OK)          ? 150 :        // fast blink on fault
        (outputPWM < 2)        ? 800 :        // slow blink at set‑point
                                 0;           // solid ON while heating
  
    if (blinkPeriod == 0) {
      digitalWrite(statusLedPin, HIGH);
    } else if (now - lastBlink >= blinkPeriod) {
      ledState = !ledState;
      digitalWrite(statusLedPin, ledState);
      lastBlink = now;
    }
  
    /* ---------- Serial Monitor ---------- */
    Serial.print("Temp: ");
    Serial.print((fault == OK) ? inputC : NAN);
    Serial.print(" °C | PWM: ");
    Serial.print(outputPWM);
    Serial.print(" | Fault: ");
    Serial.println(
        (fault == OK) ? "None" :
        (fault == OVER_TEMPERATURE) ? "Over-Temp" : "Sensor Error");

    // Shows temp on display
    display.fillRect(64, 0, 64, 32, SSD1306_BLACK);
    display.setTextSize(1);
    display.setTextColor(SSD1306_WHITE);
    display.setCursor(64,0);
    display.println(F(inputC));
    display.display
  }
  
  //EC11 code, runs everytime a change in position is detected
  void updateEncoder() {
    int MSB = digitalREad(EC11PinA);
    int LSB = digitalRead(EC11PinB);
  
    int encoded = (MSB << 1) | LSB;
    int sum = (lastEncocded << 2) | encoded;
  
    //Clockwise
    if (sum == 0b1101 || sum == 0b0100 || sum == 0b0010 || sum == 0b1011) {
      encoderPos += 5;
    }
    //Counter-Clockwise
    if (sum == 0b1110 || sum == 0b0111 || sum == 0b0001 || sum == 0b1000) {
      encoderPos -= 5;
    }
  
    lastEncoded = encoded
  }
  ~~~

</details>

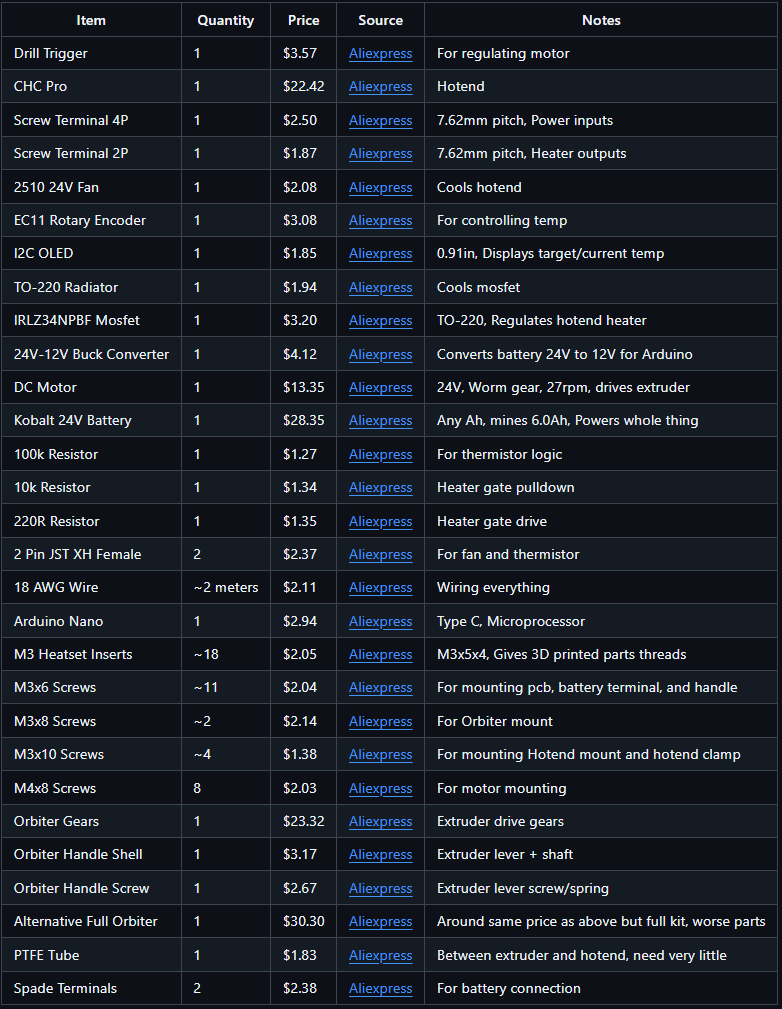
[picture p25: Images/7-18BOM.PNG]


BOM

## July 18th: Got all the documentation set up, added a knob, and made a small correction to the PCB. (3 hours)
Today was mostly spend getting all the documentation ready for submission. During this process I noticed a couple things to correct. I added a knob to the rotary encoder, and fixed an issue with the DRC on the PCB. For documentation, I wrote basically the whole README, got final images/renders uploaded, made a wiring diagram, uploaded CAD files and code, and licenced the Github with MIT license.



Wiring Diagram



Render

## July 28th: Added pullup resistors to I2C(oops), found Amazon links for faster shipping and updated BOM file with these new links, ordered everything. (3 hours)
I realized I forgot to add pullup resistors to the I2C pins, so I went in and did that. I also updated the pictures and files with these corrections. I also had to find Amazon links for a lot of the parts to get faster shipping, and updated the BOM file accordingly. I finally ordered everything and did all the stuff associated with that.


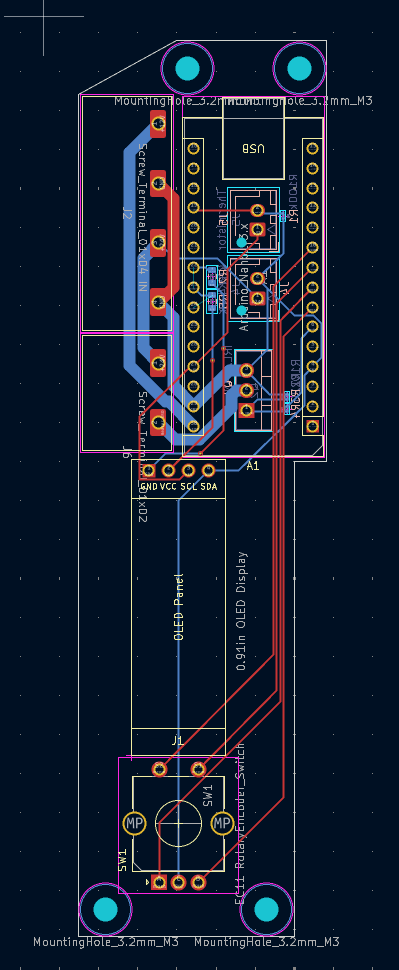
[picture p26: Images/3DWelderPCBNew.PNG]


New PCB

## August 4-6th: Printed a bunch of parts and soldered the PCB! (6 hours)
The last few days I printed out most of the parts I need for assembly, and did some of the heatset inserts. I soldered the PCB, but it turns out I accidentally put the wrong size resistors for some of the footprints, so I had to do some sketchy hand soldering. I also wired up the buck converter, and set it up for the battery. Everything was kinda done randomly so I decided to combine it into one session.

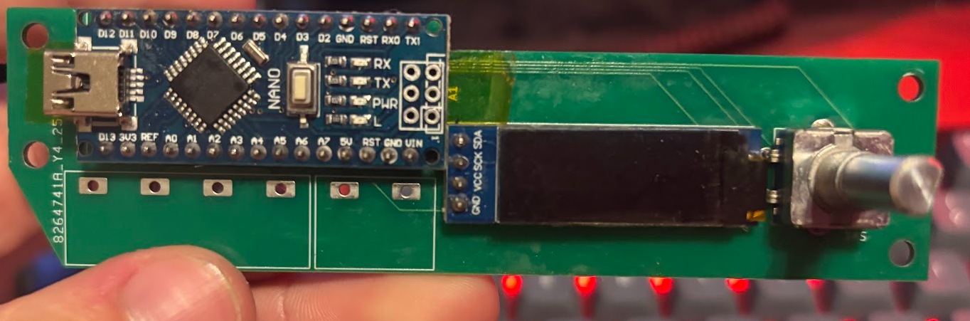
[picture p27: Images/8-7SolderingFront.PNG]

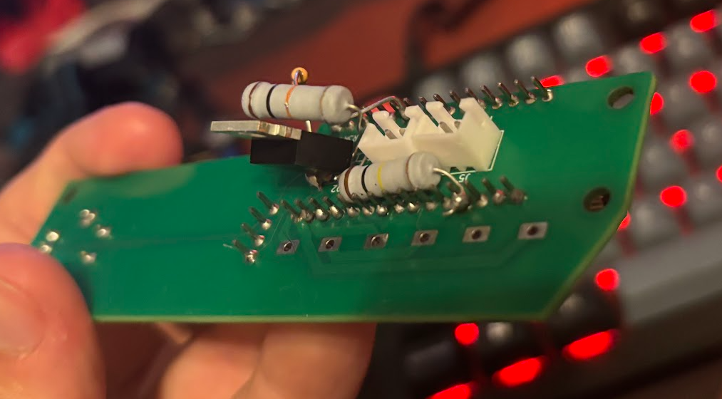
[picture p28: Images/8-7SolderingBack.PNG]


My beautiful soldering

## August 7th: First mock up assembly and fixing some mistakes... ( 6 hours)
Oh boy, I made a few more mistakes on this thing than I should have... So today I went into the pcb design to fix up the wrong size resistors I mentioned yesterday... and well I noticed that I wired my screen to the wrong pins on the Nano. Unfortunately I can't really quick fix this, so I guess this thing is going to be fixed temp for the time being. During the mock up I realized that the motor assembly I ordered off Amazon to ship faster had the motor part offset on the other side of the original one, so it interferes a little bit. I also corrected the size of a heatset insert hole and added a little extra room in the battery area to fit the buck converter. Other than that though, everything is going well. I was able to confirm the trigger/motor work with the battery, so that's good. Printing out new parts right now. I'm so mad about that PCB, but I'm just gonna order a new one I think. It won't get here in time for August 14th demo but I'm just gonna try to demo without it.



Corrected PCB

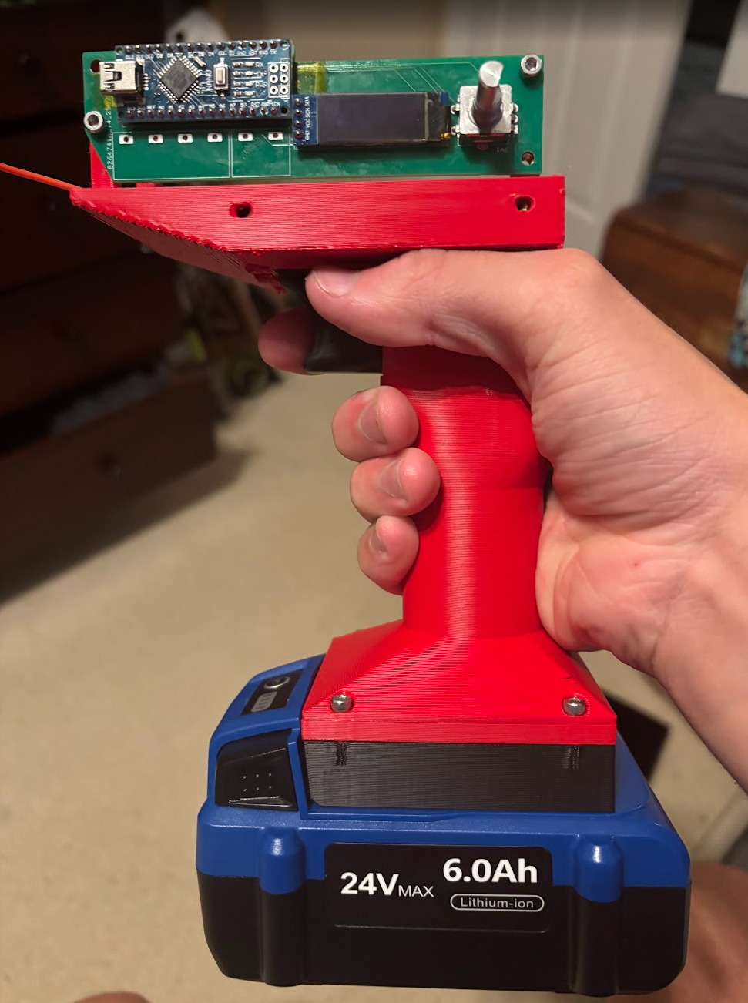
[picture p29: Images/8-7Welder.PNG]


Mock Up

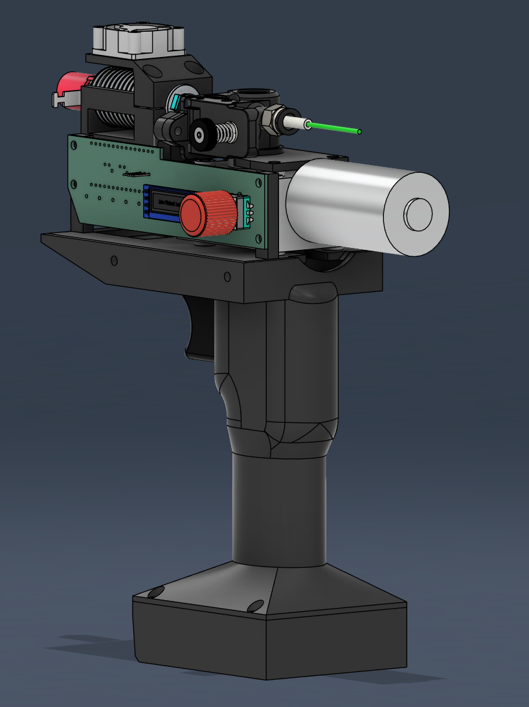
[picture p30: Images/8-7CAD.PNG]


Updated CAD

## August 9/10th: Trying to get this thing to work. (8 hours):
Well, I don't know if this project is going to work. Today I failed at getting the screen to work, got the rotary encoder working, failed to get the thermistor working, fried my Arduino, and got the new parts printed. Alright so heres the rought timeline of events. First I got those parts printed, installed heatset inserts, went great. Then I got the rotary encoder working, took a little while to get a reliable setup, but good. Then I tried to jerry-rig the screen to work, but it just wasn't working, oh well. Then I tried to get the thermistor to work... It just wasn't working, like it would always read -60C. Troubleshooting this and the screen went on for a while, but eventually the Arduino just died on me, I don't really know what happened, but yeah. I'm pretty defeated at this point. I'm just gonna have to restart from scratch, and hope I can figure it out. I'm gonna order a new screen, encoder, and some resistors to help me with trying to rebuild this thing.

## August 13/14th: Rebuilding! (8 hours):
Finally!!! It's working. This was quite a marathon. I started off with soldering up a new PCB, doing the jerry-rigged fixes as I went to make everything a bit cleaner. Then came the troubleshooting, There was a lot of troubleshooting. I just couldn't get the Arduino to connect to my PC, so I looked in the Aliexpress reviews, and sure enough, it was the wrong chipset. They sold an ATMEGA328PB under the regular P name. This basically meant there was not built in support for flashing it, and I had to figure that out. I tried a bunch of different methods, but eventually found one that worked. Use a custom Arduino board library for it, and when flashing, hold down the reset button, plug it in, flash it, then while flashing release the boot button. And the serial had to be closed. After I got that working, it was relatively smooth sailing. I did some troubleshooting the thermistor first, and realized I had the wrong value resistor. After I fixed that, I assembled everything to get the heater up and running. Then I worked on tuning the PID to a decent point, which took a while and some fixes. Then, I troubleshot the screen a while, and eventually realized I was shorting SDA to ground, due to my misrouted pcb traces. I fixed that, and after getting the rotary encoder working and everything put together in the code, it's finally done. It actually works, and I'm going to bed. This was a long night.

## August 14th: Demo! (1.5 hours):
This took longer than I thought, but today I demoed. Basically just polished the code a little more, filmed a little video of it working, and got it on Printables. I still want to finish fixing the PCB design and order that to really wrap up the project, but it's done. Thanks so much to everybody at Hack Club and Highway, this was quite the journey.



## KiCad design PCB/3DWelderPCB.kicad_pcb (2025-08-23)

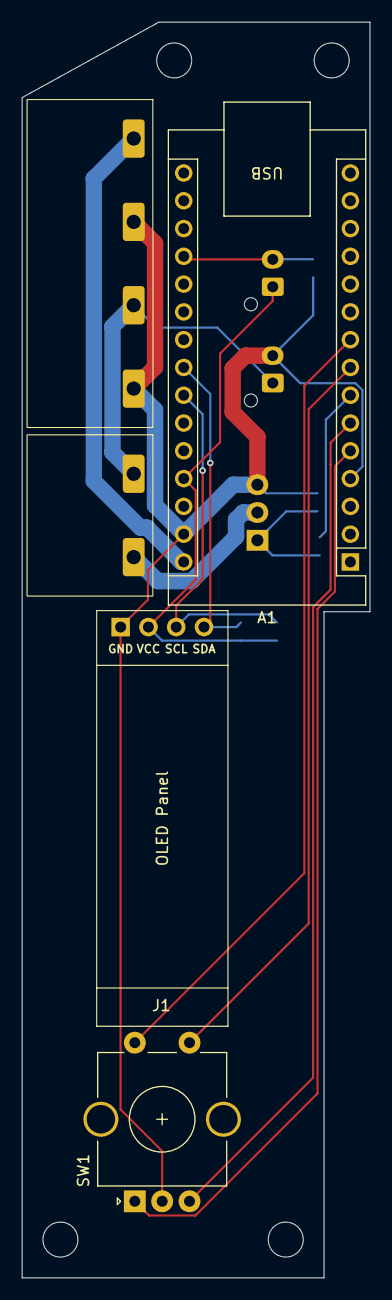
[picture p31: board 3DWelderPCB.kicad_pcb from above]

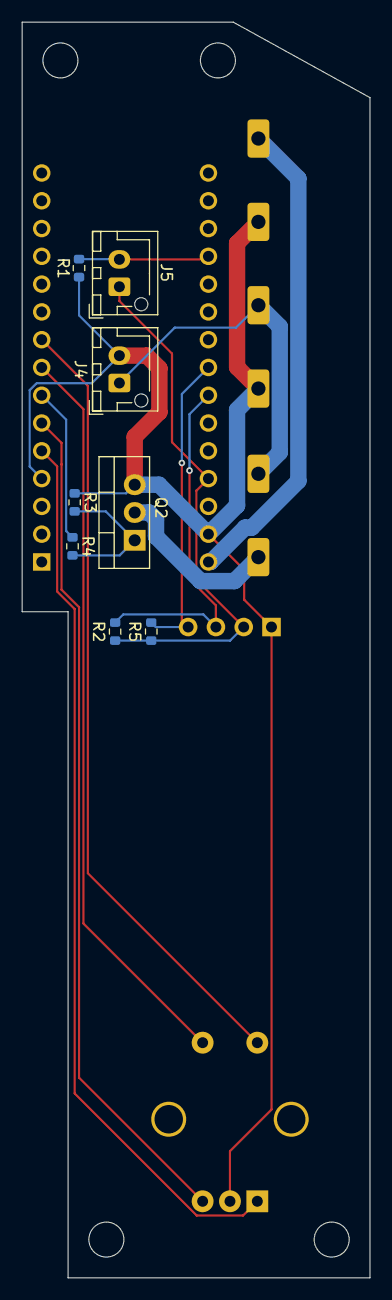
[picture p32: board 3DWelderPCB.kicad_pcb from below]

Board: 2 copper layers, 31.8 x 114.8 mm, 13 parts (8 on the bottom side), 14 nets.

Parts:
A1: Arduino_Nano_v3.x; Arduino_Nano
J1: 0.91in OLED Display; SSD1306-0.91-OLED-4pin-128x32
J2: Screw_Terminal_01x04 IN; Screw Terminal 4 Pin 7.62mmP
J4: 24V Fan; JST_XH_B2B-XH-AM_1x02_P2.50mm_Vertical
J5: Thermistor; JST_XH_B2B-XH-AM_1x02_P2.50mm_Vertical
J6: Screw_Terminal_01x02; Screw Terminal 2 Pin 7.62mmP
Q2: IRLZ34N; TO-220-3_Vertical
R1, R2, R5: 4.7K; R_0603_1608Metric
R3: R10k; R_0603_1608Metric
R4: R220; R_0603_1608Metric
SW1: EC11 RotaryEncoder_Switch; RotaryEncoder_Alps_EC11E-Switch_Vertical_H20mm_CircularMoun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

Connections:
+5V: A1.27 (+5V), J1.2, J5.1, R2.2, R5.2
+12V: A1.30 (VIN), J2.1
+24V: J2.3, J4.1, J6.1
EC11A: A1.5 (D2), SW1.A
EC11B: A1.6 (D3), SW1.B
EC11SWA: A1.8 (D5), SW1.S1
EC11SWB: A1.9 (D6), SW1.S2
GND: A1.4 (GND), A1.29 (GND), J1.1, J2.2, J2.4, J4.2, Q2.3 (S), R1.1, R3.1, SW1.C
Heater: A1.7 (D4), R4.1
Heater GND: J6.2, Q2.2 (D)
unnamed: Q2.1 (G), R3.2, R4.2
SCL: A1.24 (A5), J1.3, R2.1
SDA: A1.23 (A4), J1.4, R5.1
Thermistor: A1.19 (A0), J5.2, R1.2

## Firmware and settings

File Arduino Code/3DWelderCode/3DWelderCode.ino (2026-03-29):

#include <PID_v1.h>
#include <Wire.h>
#include <Adafruit_GFX.h>
#include <Adafruit_SSD1306.h>
#include <math.h>

#define SCREEN_WIDTH 128
#define SCREEN_HEIGHT 32
#define OLED_ADDR 0x3C

#define THERMISTOR_PIN A0
#define RELAY_PIN 3

Adafruit_SSD1306 display(SCREEN_WIDTH, SCREEN_HEIGHT, &Wire);

double Setpoint = 200; // Initial target temp
double Input, Output;

double Kp=3.0, Ki=0.05, Kd=0; // tuning parameters
PID myPID(&Input, &Output, &Setpoint, Kp, Ki, Kd, DIRECT);
int WindowSize = 300;
unsigned long windowStartTime;

const int EC11PinA = 5;
const int EC11PinB = 4;

volatile int encoderPos = 0;
int displayPos = 0;

volatile uint8_t prevState = 0; // Previous stable state of encoder

// Lookup table for encoder
const int8_t table[16] = {
  0, -1, 1, 0,
  1, 0, 0, -1,
  -1, 0, 0, 1,
  0, 1, -1, 0
};

// Thermistor settings
const float SERIES_RESISTOR = 4700.0; // Bottom resistor resistance
const float R0 = 100000.0; // Thermistor resistance at T0
const float T0_K = 25.0 + 273.15; // Room temp
const float B_COEFFICIENT = 4267.0; // Beta value (good starting point for 104GT-2)

int readADCavg(int pin, int samples = 64) {
  long sum = 0;
  for (int i = 0; i < samples; i++) {
    sum += analogRead(pin);
    delayMicroseconds(100);
  }
  return (int)(sum / samples);
}

// Steinhart–Hart coefficients for Semitec 104GT‑2
const float A = 1.009249522e-3;
const float B = 2.378405444e-4;
const float C = 2.019202697e-7;

float getTemperatureC() {
  int adcValue = readADCavg(THERMISTOR_PIN, 128); // 128 samples to smooth
  float adc = (float)adcValue;

  if (adc <= 2)  { Serial.println("ADC too low — check wiring!");  return NAN; }
  if (adc >= 1021){ Serial.println("ADC too high — check wiring!"); return NAN; }

  float Rtherm = SERIES_RESISTOR * (1023.0 / adc - 1.0);

  // Beta formula: T = 1 / ( (1/B) * ln(R/R0) + 1/T0 )
  float lnR = log(Rtherm / R0);
  float invT = (1.0 / B_COEFFICIENT) * lnR + (1.0 / T0_K);
  float Tk = 1.0 / invT;
  float Tc = Tk - 273.15;

  // Debug output
  Serial.print("ADC=");
  Serial.print(adcValue);
  Serial.print(" R=");
  Serial.print(Rtherm, 1);
  Serial.print("Ω T=");
  Serial.print(Tc, 2);
  Serial.println("C");

  return Tc;
}


void setup() {
  Serial.begin(250000);
  pinMode(EC11PinA, INPUT_PULLUP);
  pinMode(EC11PinB, INPUT_PULLUP);
  pinMode(RELAY_PIN, OUTPUT);

  prevState = (digitalRead(EC11PinA) << 1) | digitalRead(EC11PinB); // Initialize prevState

  // Enable pin change interrupts for pins 4 and 5
  PCICR |= (1 << PCIE2); // PCIE2: enables pin change interrups for port D (0-7) within PCICR: pin change interrupt control register
  PCMSK2 |= (1 << PCINT20); // Basically enables PCINT20: Pin 4 inside of PCMSK2: pin change mask register for port D
  PCMSK2 |= (1 << PCINT21); // PCINT21: Pin 5

  analogReference(DEFAULT); // Using 5V as ADC reference

  windowStartTime = millis();
  Setpoint = encoderPos;
  Input = 0; Output = 0;

  myPID.SetOutputLimits(0, WindowSize);
  myPID.SetSampleTime(1000); // 1 sec sample time
  myPID.SetMode(AUTOMATIC);

  Serial.println("Controller ready");

  if(!display.begin(SSD1306_SWITCHCAPVCC, OLED_ADDR)) {
    Serial.println(F("SSD1306 allocation failed"));
    for(;;);
  }
  display.clearDisplay();
  display.setTextSize(1);
  display.setTextColor(SSD1306_WHITE);
  display.setCursor(0,0);
  display.println("Hello World!");
  display.display();
}


void loop() {
  noInterrupts(); // prevents value from getting corrupted by state change
  int pos = encoderPos;
  interrupts();

  if (pos != displayPos) {
    displayPos = pos;
    Serial.print("Position: ");
    Serial.println(displayPos);
  }
  Setpoint = displayPos;

  float temp = getTemperatureC();

  if (isnan(temp)) return; // Skip PID if bad reading
  Input = temp;

  myPID.Compute();
  // Turn the output pin on/off based on pid output
  if (millis() - windowStartTime > WindowSize) { // Time to shift the Relay Window
    windowStartTime += WindowSize;
  }
  if (Output > millis() - windowStartTime) {
    digitalWrite(RELAY_PIN, HIGH);
    //Serial.println("Heater ON");
  } else {
    digitalWrite(RELAY_PIN, LOW);
    //Serial.println("Heater OFF");
  }

  bool heaterOn = (Output > (millis() - windowStartTime));

  // Debug: see what PID is doing
  double error = Setpoint - Input;
  //Serial.print("SP="); Serial.print(Setpoint,1);
  //Serial.print(" PV="); Serial.print(Input,1);
  //Serial.print(" ERR="); Serial.print(error,1);
  //Serial.print(" OUT(ms)="); Serial.print(Output,0);
  //Serial.print(" HEATER="); Serial.println(heaterOn ? "ON" : "OFF");

  updateDisplay();
}


ISR(PCINT2_vect) { // Triggers when encoder state changes
  uint8_t MSB = digitalRead(EC11PinA);
  uint8_t LSB = digitalRead(EC11PinB);
  uint8_t state = (MSB << 1) | LSB;

  // Combine previous and current state to get table index
  uint8_t index = (prevState << 2) | state;
  int8_t movement = table[index];

  // Only count full detents (4 steps)
  static int stepCount = 0;
  stepCount += movement;
  if (stepCount >= 4) {
    encoderPos += 5; // CW
    stepCount = 0;
  } else if (stepCount <= -4) {
    encoderPos -= 5; // CCW
    stepCount = 0;
  }
  prevState = state;
}


void updateDisplay() {
  display.clearDisplay();
  display.setTextSize(3);
  display.setTextColor(SSD1306_WHITE);
  display.setCursor(0,8);
  display.println(int(Input));
  display.setCursor(64,8);
  display.println(int(Setpoint));
  display.display();
}

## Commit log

2025-07-27 Add step file
    [3DWelderstep.step]
2025-08-08 Added new pcb, gerber, cad, pictures
    [3DWelderBatteryAdapterV2.stl, 3DWelderCHCProClamp.stl, 3DWelderCHCProMount.stl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]
2025-08-08 Updated CAD
    [3DWelderHandleV3.stl, 3DWelderSTEPV3.step]
